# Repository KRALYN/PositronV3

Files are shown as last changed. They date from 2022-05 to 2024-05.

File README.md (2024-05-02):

  

<p align="center">
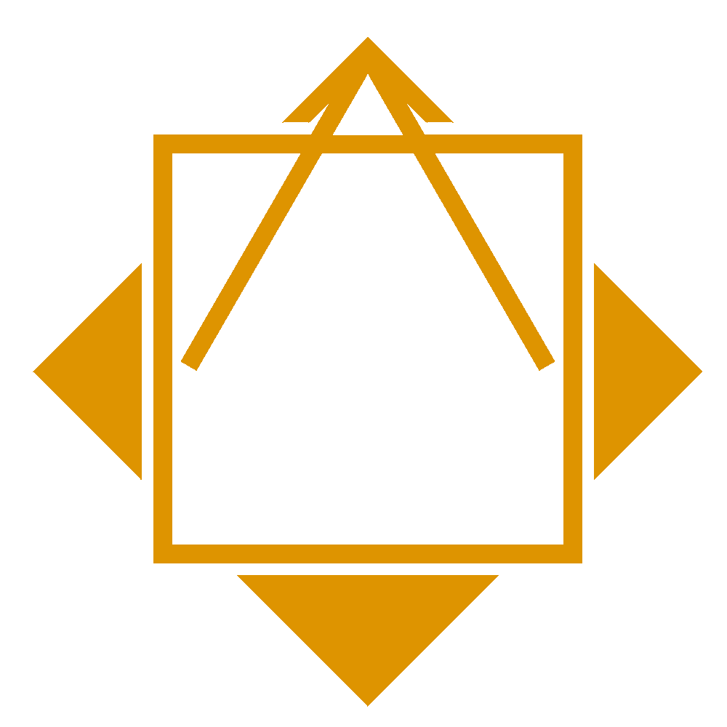
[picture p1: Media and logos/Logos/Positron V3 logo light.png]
   
</p>

---

# This Repo is now set to "LEGACY"
What does this Mean? - The Positron Project has evolved! We now partner with LDO to produce kits for the new and imporved Positron V3.2

This repo will no longer be updated, and will be moved to [the new Github Repo](https://github.com/Positron3D/Positron) once all files are made available from LDO.

Please join the [The Positron Discord](https://discord.gg/5VCruU6EYv) for the most direct updates, and keep an eye on [Our Website](https://positron3d.com).

# PositronV3 LINKS:::

[Positron 3D Website](https://positron3d.com)

[Check out our Youtube to see it in action!](https://www.youtube.com/watch?v=X_QLxTVtyng)

[Source Parts and links from here (BOM)](https://docs.google.com/spreadsheets/d/1M--jvOxUEVNc-NtEsor3uPZQsdXsPD1CKWxmc8fwLWI/edit?usp=sharing) or check out the [Alpha Wiki BOM](https://wiki.positron3d.com/books/general-information-getting-started/page/bill-of-materials-self-sourcing-guide)

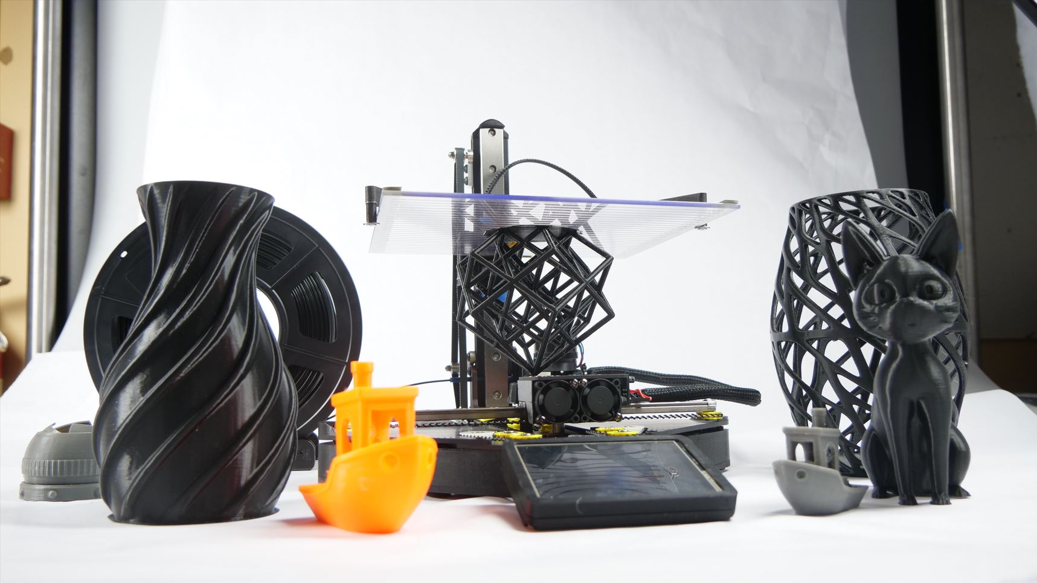
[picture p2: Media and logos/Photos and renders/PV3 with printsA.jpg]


Upside-down, compact, portable, and super fast 3D printer - `Positron V3` has it all. A compact 3D printer that packs into a filament spool box, so you can take it anywhere you want. This design is looking at a 3D printer less like a stationary machine, but more like a powerful tool in a maker/inventor's tool kit. The printer deploys and folds up in less than 90 seconds, fits easily inside a bag, and prints at 200+mm/s.

**Specs**: 
- Max Print Speed: `250mm/s`
- Max Travel Speed: `350mm/s`
- Acceleration: `9800mm/s^2`
- Build Volume: `180x185x180mm`
- Weight: `2700-3100g`
- Hotend max temp: `250C`
- Build Plate Max temp: `90C`
- Power supply: `19-24V; 150-220W`

> Do not treat this design as a finished product. Instead, please see it as a project to be improved upon. When you make this, if you find any improvements, please share it with the community! We could easely have overlooked things; Lets make this printer the best it can be!

>**Disclaimer**: `Positron V3` design is a ***functional*** prototype, not a complete product. **There is absolutely no warranty, and you will make this design at your ***OWN*** risk. We will not be responsible for any damages associated with this design**. 

If you like this design, please consider supporting the Positron 3D team via donations; [Paypal](https://donate.positron3d.com)

# Licenses



**License usage**: `CC-BY`

If you are manufacturing this 3D printer or a close derivative, please put `Positron Logo` visibily on your product and designate `Positron3D` as the inventor of this product. You can find the file inside the logos folder.

On any online postings for any Parts or Kits, please be sure to link back to this github page, as well as to Positron 3D's website.
`https://github.com/KRALYN/PositronV3`
`https://positron3d.com/`

If you made a profit from this design, please consider donating a portion to `Positron3D`. We will be exceedingly grateful.

***All hardware materials and designs provided here are licensed under the [CC-BY-SA-4.0](https://creativecommons.org/licenses/by-sa/4.0/) hardware license.
All documentation, including the Wiki, is under the Creative Commons [CC-BY-SA-4.0](https://creativecommons.org/licenses/by-sa/4.0/) license***.

<div align="center">
Open Licenses
</div>

[Top](#positronv3)

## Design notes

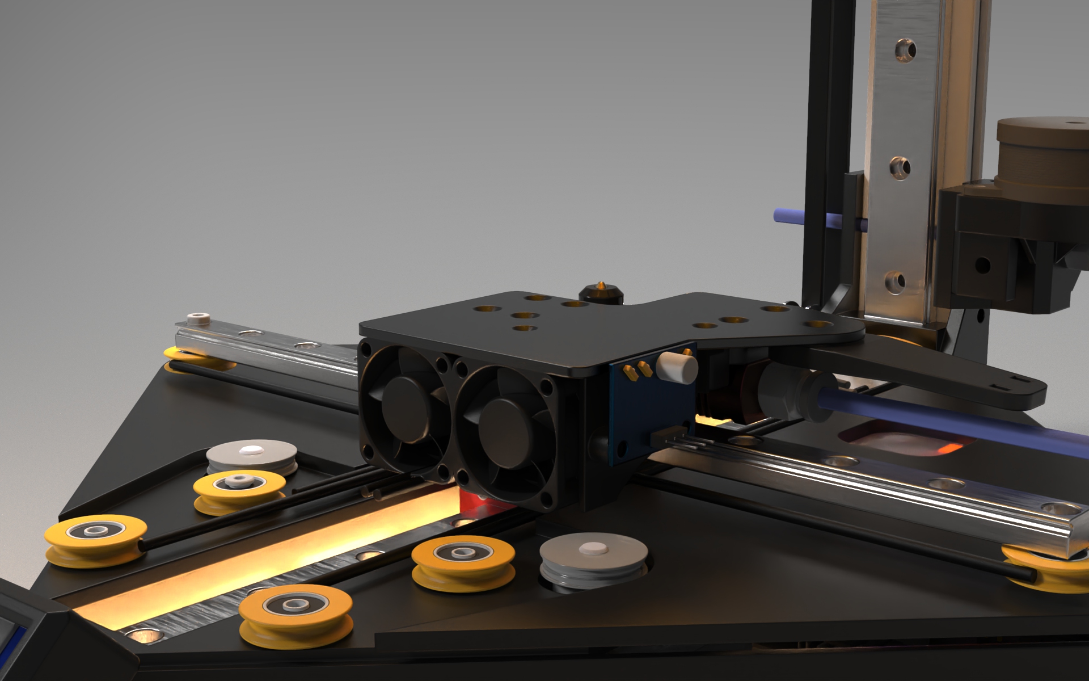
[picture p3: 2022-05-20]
Media and logos/Photos and renders/Postron V3 Render Rev B.656.jpg

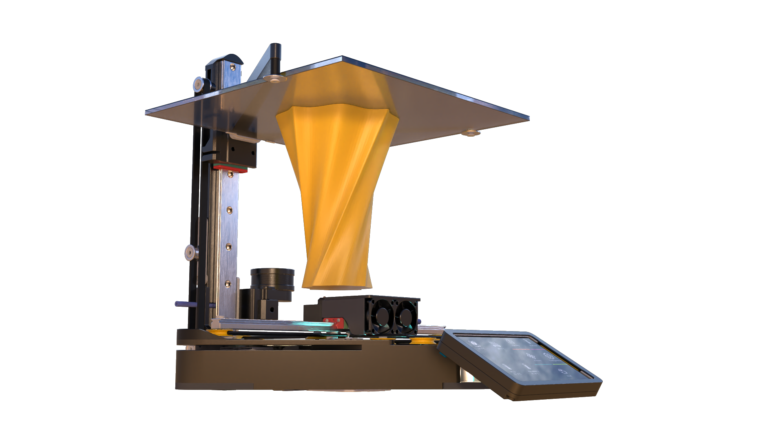
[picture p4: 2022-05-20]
Media and logos/Photos and renders/POSTRON V3 .662.png

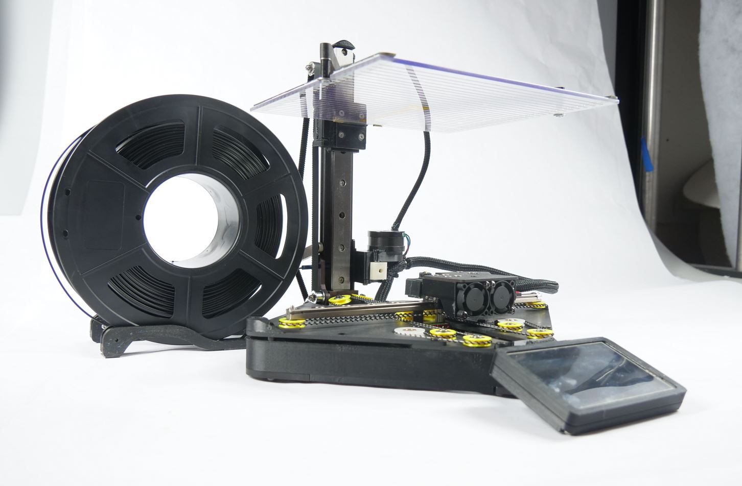
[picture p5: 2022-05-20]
Media and logos/Photos and renders/PV3 Bed High.jpg

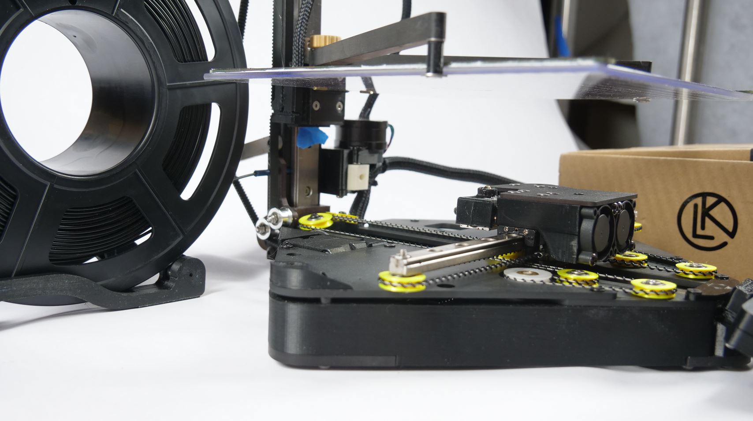
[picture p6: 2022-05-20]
Media and logos/Photos and renders/PV3 Close.jpg

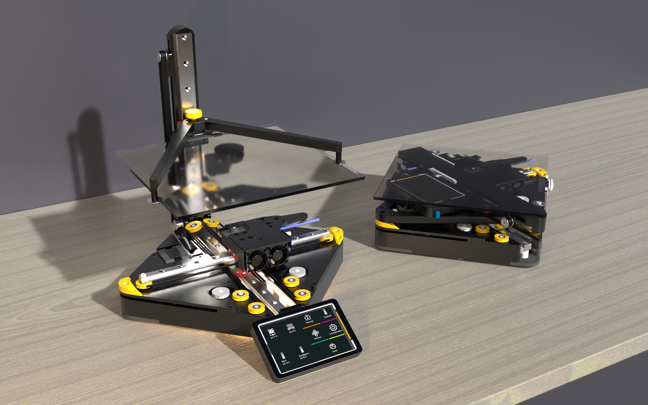
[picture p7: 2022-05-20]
Media and logos/Photos and renders/POSTRON V3 .658.jpg

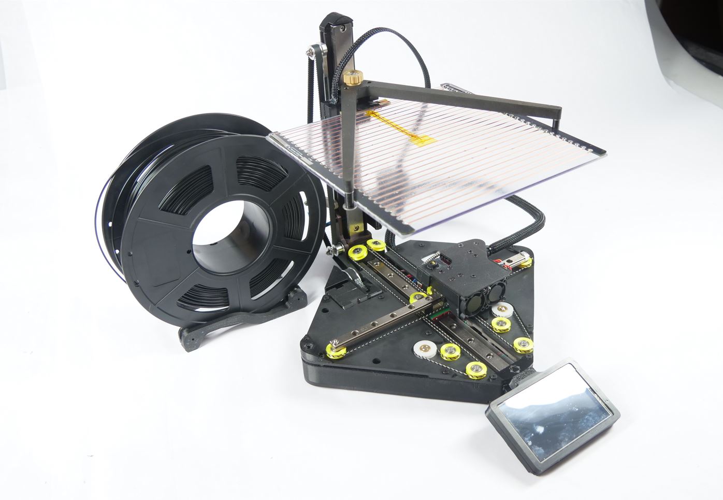
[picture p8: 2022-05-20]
Media and logos/Photos and renders/PV3 ISO.jpg

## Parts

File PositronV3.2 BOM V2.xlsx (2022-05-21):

PositronV3.2 BOM
License: CC BY |  |  | Positron V3 intro video: https://www.youtube.com/watch?v=X_QLxTVtyng
If there is any error, missing parts, or recommendations, please email kralyn3d@gmail.com |  |  |  | Prices may flucuate and not be accurate
All amazon links are affiliates,
Electronics
Number | Name | Purpose/descripton | pcs needed | Link Primary | Cost (Primary Links) | Link Alt (Cheap but slow) | Cost(Cheap but slow) | Total Cost: (Cheaper Link) | Notes:
 | SKR PICO | Control board | 1 | https://amzn.to/3Nm50Lj | 40.99 | https://www.biqu.equipment/products/btt-skr-pico-v1-0 | 28.98 (Sale) | 28.98
 | RPI/Orange Pi | Raspberry pi zero 2W | Pick one | https://www.amazon.com/Raspberry-Zero-Bluetooth-RPi-2W/dp/B09LH5SBPS | TOO EXPENSIVE Right now | https://www.adafruit.com/product/5291 | 15? |  | PLEASE FIND CHEAP SOURCE! Buy at MSRP
 |  | Raspberry pi 4 | Pick One | https://amzn.to/3lxtN37 | TOO EXPENSIVE Right now | https://www.adafruit.com/product/4295 | 30? | 15 | PLEASE FIND CHEAP SOURCE! Buy at MSRP
 |  | Raspberry pi 3 | Pick One | https://www.amazon.com/Raspberry-Pi-3-Model-B/dp/B082QN6L1N | TOO EXPENSIVE Right now | https://www.adafruit.com/product/3055 | 35? |  | PLEASE FIND CHEAP SOURCE! Buy at MSRP
 | Nema 17 20mm | X/Y motor | 2 | https://amzn.to/3G3fPQb | 29.99 | https://www.aliexpress.com/item/1005001303445983.html?ad_pvid=202205191323183466211090998200001325140_1&s=p | 10.71 | 10.71 | 16Ncm
 | Nema 14 28mm | Z Motor | 1 | https://amzn.to/3Nngkab | 21.65 | https://www.aliexpress.com/item/1005002724822207.html | 6.36 | 6.36 | 11Ncm
 | Nema 14 Round | Extruder Motor | 1 | https://amzn.to/3NmFV35 | 20.99 | https://www.aliexpress.com/item/1005002509418988.html | 16.89 | 16.89 | FYSETC 3D Printer Parts 36mm Motor Extruder Stepper Motor 1.8 Angle 0.5A
 | 3.5in TFT GPIO | Touch Screen | 1 | https://amzn.to/3wDS78P | 22.79 | https://www.aliexpress.com/item/4000213494900.html | 2.99 | 2.99
 | IDC 10 pin socket 2.54 | Touch screen connect | 1 | https://amzn.to/3G5ufPU | 5.99 | https://www.aliexpress.com/item/1005001400147026.html | 0.61 | 0.61
 | IDC 10 pin Cable 2.54 | Touch screen power transport | 1 | https://amzn.to/3LwD2LN | 7.99 | https://www.aliexpress.com/item/3256801318866388.html?s=p | 0.41 | 0.41
 | 50W heater cartridge | Heater cartige | 1 | https://amzn.to/3Lw8UjJ | 9.99 | https://www.aliexpress.com/item/2251832656974771.html?pdp_ext_f=%7B%22sku_id%22%3A%2265107791932%22%7D | 1.1 | 1.1
 | NTC 3950K | Temp sensor | 1 | https://amzn.to/3LyQ5w2 | 11.28 | https://www.aliexpress.com/item/3256804109721213.html | 2.39 | 2.39
 | IR bed Probe | IR Probe Differential IR Height Sensor | 1 | https://amzn.to/39ZIREf | 18.99 | https://www.aliexpress.com/item/2251832808870223.html?pdp_ext_f=%7B%22sku_id%22%3A%2266922445346%22%7D | 9.99 | 9.99
 | magnetic connector 6pin | Bed mounting | 1 | https://www.aliexpress.com/item/1005002669709542.html?spm=a2g0o.order_list.0.0.42ea1802lsiPKI | 3.23 |  |  | 3.23 | 90 degree type!!
 | 2510mm Fan 24V | Cooling | 3 | https://amzn.to/3Lp8Lyk | 17.99 | https://www.aliexpress.com/item/32807610078.html | 4.7 | 4.7
 | 5.5x2.1 DC Jack 8A | Power input | 1 | https://amzn.to/3Mv42MX | 7.99 | https://www.aliexpress.com/item/1005003515013042.html?s=p | 0.13 | 0.13 | Use 5.5x2.5 if your power supply is such
 | 24V 8 or 10A power supply | Power supply | 1 | https://amzn.to/3NnZmZ7 | 31.5 | https://www.aliexpress.com/item/1005001946903779.html | 38.2 | 31.5
 | Rocker Switch 10A | Power switch | 1 | https://amzn.to/3LJ4XIB | 6.99 | https://www.aliexpress.com/item/3256802987532702.html?ad_pvid=20220519143050667954035316040001501905_4&s=p | 0.22 | 0.22
 | 24V 3010 Fan Blower | Print Cooling |  | https://amzn.to/3lwK3RW | 9.99 | https://www.aliexpress.com/item/2255800894119261.html?ad_pvid=202205191435593637780472359080001143420_1&s=p | 2.85 | 2.85
 | Kapton Film Heater 200mm 100W | Bed heating Choose one | Pick One | https://www.robotdigg.com/product/877/200mm,-210mm-or-250mm-kapton-film-flexible-heater | 12 |  |  | 12
 | Copper heater strips | Frost Fighter | Pick One | https://frostfighter.com/clear-view-order-guide.htm?add-to-cart=1366&v=402f03a963ba | TOO EXPENSIVE Right now (89 dolars?) |  |  |  | Or find other strips that are 0.02Ω/in
Motion
 | MGN 9C 250mm | X axis rail | 1 | https://amzn.to/3wuJOxm | 20.99 | https://www.aliexpress.com/item/4000264234020.html | 14.72 | 14.72 | 227mm actual, low preload
 | MGN 12C 250mm | Y axis Rail | 1 | https://amzn.to/3G2VnPd | 23.99 | https://www.aliexpress.com/item/4000264234020.html | 14.72 | 14.72 | 235mm actual, low preload
 | MGW 9C 300mm | Z axis rail | 1 | https://www.robotdigg.com/product/955/MGW9-Linear-Rail-and-Carriage | 29 |  |  | 29 | 247mm actual, Medium to high preload
 | GT2 Idler 16T Smooth | Z axis | 4 | https://amzn.to/3wDXZ1R | 11.99 | https://www.aliexpress.com/item/32822906447.html?pdp_ext_f=%7B%22sku_id%22%3A%2264964440436%22%7D | 2.5 | 2.5 | 3mm bore
 | GT2 Low profile Pulley 20T | Z axis | 1 | https://www.aliexpress.com/item/32913757229.html?spm=a2g0o.order_list.0.0.2a3f1802Zv2sCI | 0.72 |  |  | 0.72
 | 48T GT2 Pulley 5mm Bore | Z axis drive train | 1 | https://amzn.to/3Nr7xEg | 12.99 | https://www.aliexpress.com/item/2251832595367020.html?pdp_ext_f=%7B%22sku_id%22%3A%2266985020229%22%7D | 0.53 | 0.53
 | 16T GT2 Pulley 5mm Bore | Z axis drive train | 1 | https://amzn.to/3Nr7xEg | 12.99 | https://www.aliexpress.com/item/2251832595367020.html?pdp_ext_f=%7B%22sku_id%22%3A%2266985020229%22%7D | 0.53 | 0.53
 | GT2 6mm Belt 750mm | Z axis drive train | 1 | https://amzn.to/39zgaOm | 9.99 | https://www.aliexpress.com/item/2251832732634187.html (https://www.aliexpress.com/item/32803353643.html?pdp_ext_f=%7B%22sku_id%22%3A%2267288271232%22%7D) | 2.99 | 2.99
 | GT2 6mm belt loop 130mm | Z axis drive train | 1 | https://amzn.to/3LvUcsL | 11.88 | https://www.aliexpress.com/item/3256803233969258.html (https://www.aliexpress.com/item/2251832785035303.html) | 0.93 | 0.93
 | 5mm Shaft L37mm | Z axis drive train | 1 | https://amzn.to/3a5FwDH | 6.49 | https://www.aliexpress.com/item/2251832241547558.html | 1.64 | 1.64
 | MF115ZZ flanged bearing | Z axis drive train | 2 | https://amzn.to/3wHxTex | 7.49 | https://www.aliexpress.com/item/1005003424591537.html | 7.95 | 7.95
 | BMG drive gear kit | 50T gear with dual gear filament drive | 1 | https://amzn.to/3wFckuN | 21.99 | https://www.aliexpress.com/item/1005001655308475.html | 3.76 | 3.76 | Diy extrder kit
 | 623ZZ Ball Bearing | for Syncromesh Pullies | 12 | https://amzn.to/3yKm5e5 | 13.49 | https://www.aliexpress.com/item/3256803986594273.html?ad_pvid=202205191520509432607776842250001534793_2&s=p | 0.66 | 0.66 | 3x4x10mm
 | Syncromesh Cable 3.81P | SDP/SI name is A 6J 9MAS0805 | 2m | https://shop.sdp-si.com/catalog/product/?id=A_6J_9MAS0805 | 6.61 |  |  | 6.61 | Offical Quote for 1000m is $3.4/m I asked
 | Syncromesh Pulley 3.81P 15T | SDP/SI name A 6P 9M0801505 | 2 | https://shop.sdp-si.com/catalog/product/?id=A_6P_9M0801505 | 22.3 |  |  | 22.3 | Offical Quote for 1000 pcs is $4.79/pcs I asked
Other Mechanical
 | Mk8 heatsink | typically on ender 3 extruder | 1 | https://spool3d.ca/creality-cr-10-heatsink/ | 9
 | Ender 3 heatbreak |  | 1 | https://amzn.to/3PvqYNW | 9.99 | https://www.aliexpress.com/item/3256803118054066.html?ad_pvid=202205191523067573433897611140001583415_1&s=p | 3.28? | 3.28?
 | E3D V6 0.4 nozzle |  | 1 | https://amzn.to/3LJjwMh | 6.59 | https://www.aliexpress.com/item/32827246895.html?pdp_ext_f=%7B%22sku_id%22%3A%2264999741077%22%7D | 0.28 | 0.28
 | capricorn bowden tubing | PTFE tube | 1 | https://amzn.to/3NoMAtp | 9.79 | https://www.aliexpress.com/item/1005001833973163.html | 3.28 | 3.28
 | PC4-M10 PTFT push connector |  | 2 | https://amzn.to/3LAA6xr | 7.99 | https://www.aliexpress.com/item/32895495458.html?pdp_ext_f=%7B%22sku_id%22%3A%2265749709218%22%7D | 0.48 | 04.48?
 | m3x10mm Spacrer Aluminum | Outer dia is 8mm | 8 | https://amzn.to/3MvXLk0 | 11.99 |  |  | 11.99 | Machine down the tube
 | Rubber feet 4mm thick | Bottom feet | 5 | https://amzn.to/3yQ7XzU | 4.98 | https://www.aliexpress.com/item/1005001688504734.html | 3.2 | 3.2
 | 200x200x3mm Borosilicate glass | headed bed body | 1 | https://amzn.to/3MzabaO | 13.99 | https://www.aliexpress.com/item/33045470605.html?pdp_ext_f=%7B%22sku_id%22%3A%2267375853971%22%7D | 14.99 | 13.99
 | 0.25in cable sleeve | need at least 1m | 1 | https://amzn.to/3yKN49n | 8 | https://www.aliexpress.com/item/2255801147284533.html?ad_pvid=202205192036512802097721304800001661795_5&s=p | 0.45 | 0.45
 | M4 ring terminal 22-16 AWG | Crimping syncromesh cable | 2 | https://amzn.to/3luzFKO | 7.99 | https://www.aliexpress.com/item/2251832619804942.html?pdp_ext_f=%7B%22sku_id%22%3A%2264378436063%22%7D | 1.99 | 1.99
 | M4x12 Dowel pin | Bed location 10-15mm acceptable | 2 | https://amzn.to/3NrBJz6 | 6.99 | https://www.aliexpress.com/item/1005003326358562.html?ad_pvid=202205192047085008116476482240002235729_2&s=p | 0.02 | 0.02
 | M3 nylon spacer assortment |  | x | https://amzn.to/3wDTWCP | 12.99 | https://www.aliexpress.com/item/1005003203012157.html?ad_pvid=202205192059301936392797174340002019319_2&s=p | 10.24 | 10.24
 | Zip ties 4in/100mm | Cable management | 2022-10-20 | https://amzn.to/3LxeJgP | 5.5 | https://www.aliexpress.com/item/2251832692914034.html?pdp_ext_f=%7B%22sku_id%22%3A%2265990744133%22%7D | 1.96 | 1.96
 | M3x15 Aluminum Spacer | Motor Mounting | 4 | Same as m3x10mm Spacrer Aluminum |  |  |  |  | Machine down the tube
Fasteners
 | M6x14 thumbscrew 19mm head dia | For Z axis bed arm mounting | 1 | https://www.amazon.com/dp/B07KPDP1HD?s=hi | 13.99 | https://www.aliexpress.com/item/32995228198.html (https://www.aliexpress.com/item/3256801661342209.html) | 2.42 | 2.42 | if you get m6x15 please shave of a mm
 | M5 washer | Z axis holder | 2 | https://amzn.to/38F9luy | 6.99 | https://www.aliexpress.com/item/3256804067235132.html?ad_pvid=20220519211700958809818633940002036878_4&s=p | 0.1 | 0.1
 | M6 nut | Thumbscrew stabilze | 2 | https://amzn.to/3wuwBnY | 3.72 | https://www.aliexpress.com/item/2251832790859685.html?ad_pvid=20220519212820351383008677750001716113_2&s=p | 0.63 | 0.63
 | M4 nut | Z axis mounts | 8 | https://amzn.to/39IXgEY | 6.49 | https://www.aliexpress.com/item/1005001966426139.html | 1.05 | 1.05
 | M4x10 Buttonhead |  | 12 | https://amzn.to/3wBeZG8 | 9.5 | https://www.aliexpress.com/item/32918136753.html?pdp_ext_f=%7B%22sku_id%22%3A%2265960267709%22%7D | 1.39 | 1.39
 | M4x8 buttonhead |  | 2 | https://amzn.to/3LDHVCU | 6.99 | https://www.aliexpress.com/item/10000148429238.html | 1.06 | 1.06
 | M3x6 buttonhead | Find a M3 buttonhead kit | 11
 | M3x20 Buttonhead | Find a M3 buttonhead kit | 2
 | M3x14 Buttonhead | Find a M3 buttonhead kit | 2 | https://amzn.to/3Lq0Fpe | 16 | https://www.aliexpress.com/item/32967225441.html | 2022-02-10 | 7
 | M3x10 Buttonhead | Find a M3 buttonhead kit | 15
 | M3x8 Buttonhead | Find a M3 buttonhead kit | 12
 | M3x25 buttonhead | Find a M3 buttonhead kit | 4
 | M3x12 Buttonhead | Find a M3 buttonhead kit | 5
 | M3 nut 2.4mm | Find a M3 buttonhead kit | 35
 | M3 Washer | Find a M3 buttonhead kit | 12
 | M3x14 Waferhead | Low Wafer Head Machine Screws Flat Head Screw | 17 | https://www.ebay.com/itm/154373020371?chn=ps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 | 2 |  |  | 2
 | M3x12 Waferhead | Low Wafer Head Machine Screws Flat Head Screw | 2 | https://www.ebay.com/itm/154373020371?chn=ps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 | 2 |  |  | 2
 | M3x12 Flathead | Find a M3 Flathead kit | 8
 | M3x18 flathead | Find a M3 Flathead kit | 8
 | M3x10 Flathead | Find a M3 Flathead kit | 1 | https://amzn.to/3wxvXXa | 12.79 | https://www.aliexpress.com/item/32968616563.html | 2022-01-05 | 5
 | M3x6 Flathead | Find a M3 Flathead kit | 2
 | M3x23 Flathead | Can be cut down from M3x25 | 2
 | M3 Nylock Nut | Optional? with thread locker | 2 | https://amzn.to/3wvFwWv | 6.99 | https://www.aliexpress.com/item/2251832799467001.html?ad_pvid=202205192226593765816299021670002129150_1&s=p | 2.07 | 2.07
 | M2.5x8 Flat head |  | 2 | https://amzn.to/3LvfarR | 8.67 | https://www.aliexpress.com/item/3256803068882172.html?ad_pvid=202205192233051883260506929100002345825_4&s=p (https://www.aliexpress.com/item/32900755820.html?ad_pvid=202205192233051883260506929100002345825_3&s=p) | 2.39 | 2.39
 | M2x10 Buttonhead | For Screen | 4 | https://amzn.to/3MzglHU | 6.99 | https://www.aliexpress.com/item/3256803068882172.html?ad_pvid=202205192233051883260506929100002345825_4&s=p | 1.99 | 1.99
 | M3x8 Sockethed | Find a M3 Sockethead kit | 5
 | M3x30 Sockethead | Find a M3 Sockethead kit | 2 | https://amzn.to/3G404bR | 22 | https://www.aliexpress.com/item/2255799876641488.html | 5.72 | 5.72
 | M3x20 Sockethead | Find a M3 Sockethead kit | 7
 | M3x6 threaded insert | Heat press plastic insert | 5 | https://amzn.to/3LxL4UH | 14.99 | https://www.aliexpress.com/item/3256802429609058.html?ad_pvid=202205192244399748035622216640002420224_4&s=p | 2.62 | 2.62
Raw materials/Stock
 | 200x200x4mm AL plate | 6061, 8x8in also works, thickness can be 0.16in | 1 | https://amzn.to/3yTJUAh | 22.99 | https://www.aliexpress.com/item/3256801094393303.html?ad_pvid=202205192158586959024232090060002022455_1&s=p | 16.74 | 16.74 | For base plate and z axis brackets
 | 100x100x2mm AL plate | 6061 T6 | 1 | https://amzn.to/3a1jDFy | 17.99 | https://www.aliexpress.com/item/1005004280302089.html?ad_pvid=202205192158586959024232090060002022455_3&s=p | 4.51 | 4.51 | For Hotend cover and extruder mounting
 | 120x180x3mm AL Plate | 6061 T6 | 1 | https://amzn.to/382e4pT | 16.99 |  |  | 16.99 | For Motor Mounts
 | 220x220x10mm AL plate | 3/8in also works | 1 | https://www.amazon.com/ALUMINUM-SOLID-T6511-Stock-Plate/dp/B01F80W35Q | 30.69 |  |  | 30.69 | For bed arm, bed arm is stackable
 | 30x30x5mm AL angle 90 degree | only 32mm needed | 1 | https://us.misumi-ec.com/vona2/detail/110300466930/?Tab=wysiwyg_area_0 | 7.72 |  |  | 7.72
 | 3010 x250mm AL extrusion | Special, only MISUMI has it. Z axis | 1 | https://us.misumi-ec.com/vona2/detail/110302261730/?Tab=wysiwyg_area_0 | 2.91 |  |  | 2.91 | HFSQN4-1030-250
 | 3mm Black acrylic sheet | 200x300 sheet Sand blasted finish | 1 | https://amzn.to/3Mwj6Kk | 16.95 |  |  | 16.95 | 0.125in also works
 | 3mm Clear Acrylic sheet | 200x60mm Sheet. Sand blasted | 1 | https://amzn.to/3lq6gBt | 13.68 |  |  | 13.68 | 0.125in also works
 | Aluinum Block 6061 | MISC macheing 40x40x70 bar | 1 | https://amzn.to/3wI5uVH | 22.99 |  |  | 22.99
3D printed Parts
 | 3D printed toolhead interconnect | ABS. Prefer SLS nylon | 1
 | Belt and Connector Holder | ABS | 1
 | Edge Raised clamp(Mirror) | PLA/ABS/PETG | 1
 | Edge Raised clamp | PLA/ABS/PETG | 1
 | End Holder Block | ABS/PETG | 1
 | EXP Connector Holder | ABS/PETG | 1
 | Extruder Base | ABS | 1
 | Extruder Cap | ABS | 1
 | Extruder Mid body | ABS | 1
 | Extruder Silder Arm | ABS | 1
 | LED Holder Body | PLA/ABS/PETG | 1
 | Light Clamp Holder | PLA/ABS/PETG | 1
 | M4 spacer 4.1mmx6 | PLA/ABS/PETG | 1
 | Pulley Holder Bottom | ABS/PETG | 1
 | Pulley Holder Top | ABS/PETG | 1
 | Screen holder Base | PLA/ABS/PETG | 1
 | Screen Holder Lid | PLA/ABS/PETG | 1
 | Side Panel Left | PLA/ABS/PETG | 1
 | Side Panel Right | PLA/ABS/PETG | 1
 | Thumbscrew body 3D printed | PLA/ABS/PETG | 1
 | Top Panel Spacers | PLA/ABS/PETG | 1
 | Z axis top stopper | PLA/ABS/PETG | 1
 | 15mm pDia Synchromesh | Prefer Lathed out of Delrin | 10
 | 19.5mm pDia Synchromesh | Prefer Lathed out of Delrin | 2
 | Silicone Mold Bottom (1) | PETG, For hotend Silicone Mold | 1
 | Silicone Mold Bottom | PETG, For hotend Silicone Mold | 1
 | Silicone Mold Top | PETG, For hotend Silicone Mold | 1 |  |  |  |  | 20 | Estimated 3D print material cost
 | JLCPCB Customn PCB | From Github | 1 |  |  |  |  | 35 | around 35 dollars plus SMT
 |  |  |  |  |  |  | Total Cost Estimated: | 532.64 | Dollars | Does not take into account shipping, wires, connectors, materials, time etc

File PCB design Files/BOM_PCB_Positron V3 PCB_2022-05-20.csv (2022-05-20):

ID | Name | Designator | Footprint | Quantity | Manufacturer Part | Manufacturer | Supplier | Supplier Part | Price
1 | XH-2AW_C2908611 | CN3 | CONN-TH_XH-2AW_C2908611 | 1 | XH-2AW | HCTL(华灿天禄) | LCSC | C2908611 | 0.006
2 | 610-92-05GB00 | EXP-10P | CONN-TH_610-92-05GB00 | 1 | 610-92-05GB00 | PINREX | LCSC | C390692 | 0.013
3 | XH-4AW_C2908613 | CN4 | CONN-TH_XH-4AW | 1 | XH-4AW | HCTL(华灿天禄) | LCSC | C2908613 | 0.011
4 | 100nF | C1 | C0603 | 1 | CC0603KRX7R9BB104 | YAGEO | LCSC | C14663 | 0.002
5 | WF2541-WS10E01 | CN1 | CONN-TH_WF2541-WS10E01 | 1 | WF2541-WS10E01 | Wcon(维峰电子) | LCSC | C721503
6 | WS2812B-B/W | LED1,LED2,LED3,LED4,LED7 | LED-SMD_4P-L5.0-W5.0-TL_WS2812B-B | 5 | WS2812B-B/W | worldsemi | LCSC | C2761795 | 0.121
7 | 19-213/Y2C-CQ2R2L/3T(CY) | LED6 | LED0603-R-RD | 1 | 19-213/Y2C-CQ2R2L/3T(CY) | EVERLIGHT | LCSC | C72038 | 0.026
8 | InputHeader | P1,P3 | HEADER-PINS_2.54_04PIN_01ROW | 2
9 | OutputHeader | P2 | HEADER-PINS_2.54_04PIN_01ROW | 1
10 | PTH-Circle | PTH1,PTH2,PTH3,PTH4,PTH5,PTH6,PTH7,PTH8,PTH9,PTH10,PTH11,PTH12,PTH13,PTH14,PTH15,PTH16,PTH17,PTH18,PTH19,PTH20,PTH21,PTH22,PTH23,PTH24,PTH25,PTH26,PTH27 | PTH-CIRCLE.PACK | 27 | Breakout-Hole
11 | 330Ω | R1 | R0603 | 1 | 0603WAF3300T5E | UniOhm | LCSC | C23138 | 0.001
12 | PAD | U1,U2,U3,U4,U8,U9,U10,U11,U12,U13 | PADPAD | 10
13 | 1*6 2.2mmP Magnetic Pogo Pin Connector 3A | U7 | 1*6 2.2P MAGNETIC POGO PIN CONNECOTR | 1 |  |  | Aliexpress
14 | 2*15P 2.54mm copy | H1,TFT | DIP-2.54MM-2X15P | 2 | - | Shenzhen Cankemeng | LCSC | C169817 | 0.132

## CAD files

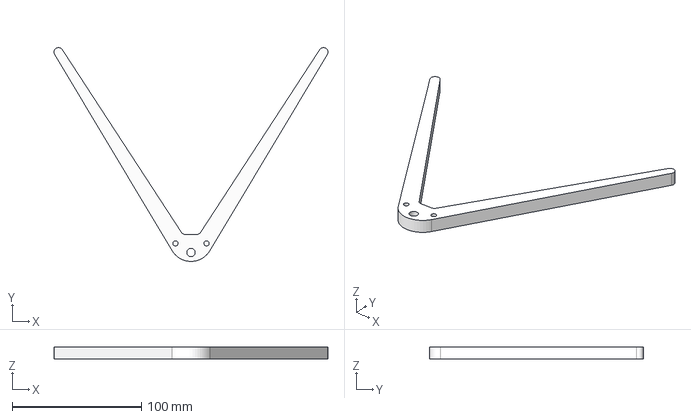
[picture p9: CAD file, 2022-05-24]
CAD files/Custom Metal Parts/Bed Holder Main.step
212.0 x 165.4 x 9.50 mm

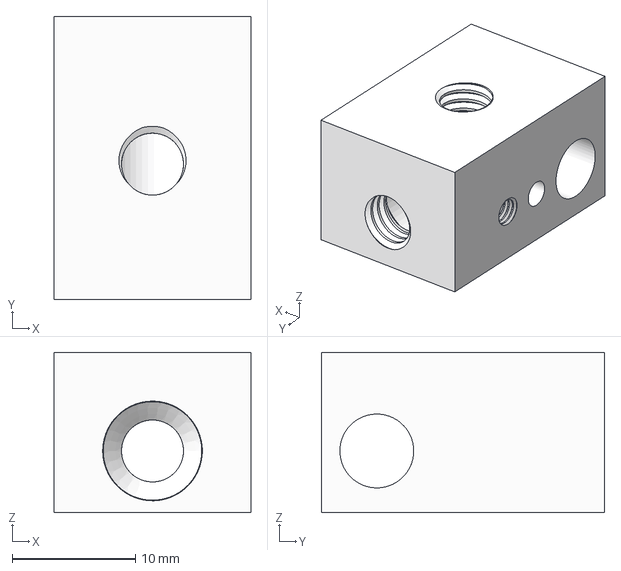
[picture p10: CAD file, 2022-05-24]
CAD files/Acrylic Panel Parts/Hotend block main body.step
16.0 x 23.0 x 13.0 mm

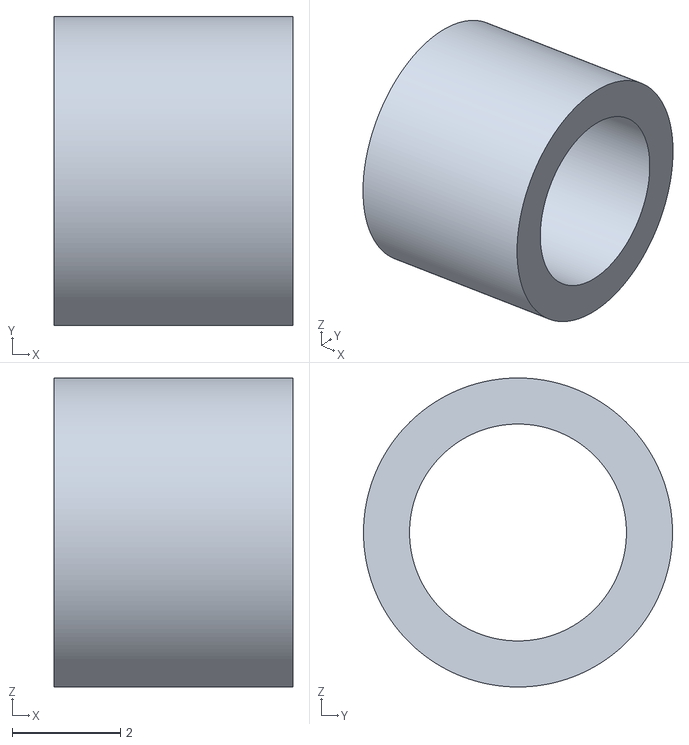
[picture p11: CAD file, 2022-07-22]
CAD files/3D printed Parts/Z axis belt tensioner arm hinge spacer.stl
4.40 x 5.70 x 5.70

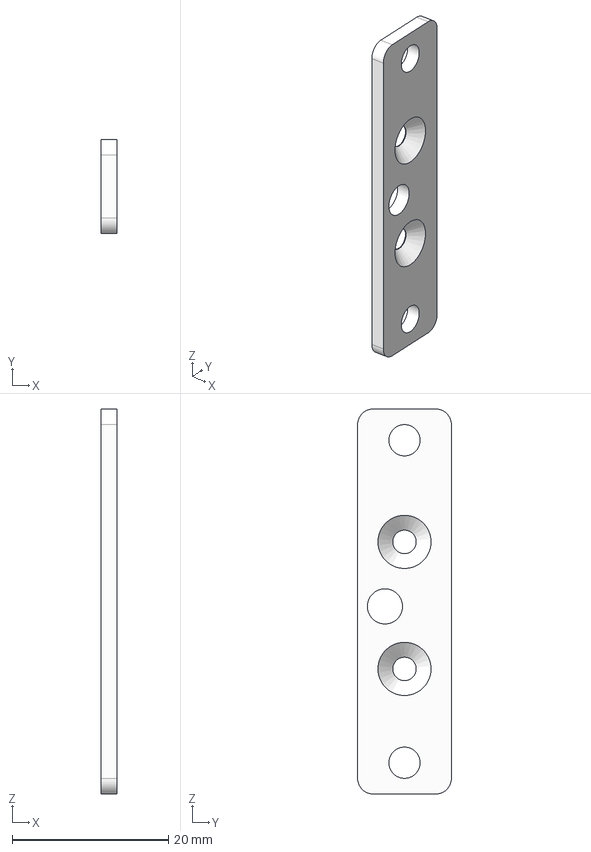
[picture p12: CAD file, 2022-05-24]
CAD files/Acrylic Panel Parts/AL bracket Extruder Mounting.step
2.00 x 12.0 x 49.2 mm

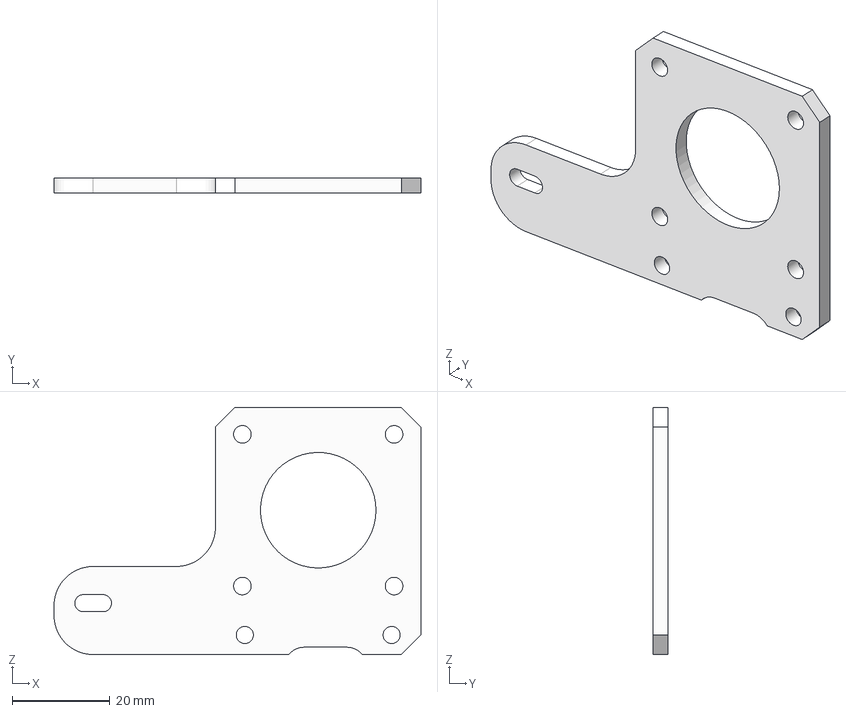
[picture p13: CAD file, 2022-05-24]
CAD files/Custom Metal Parts/Nema 17 holder M3.step
75.0 x 3.00 x 50.5 mm

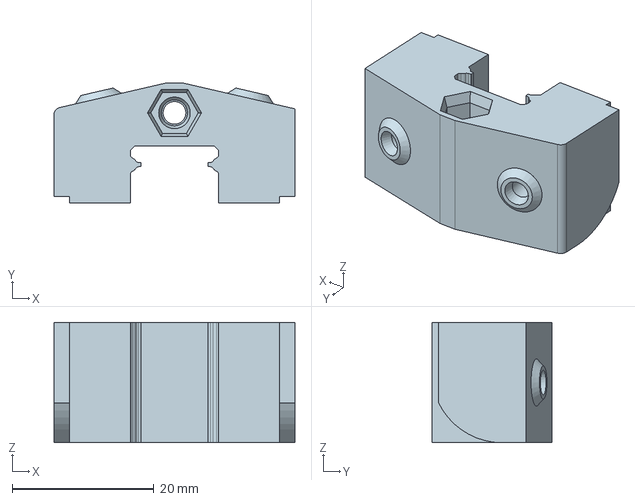
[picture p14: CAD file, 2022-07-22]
CAD files/Z axis tensioner mod/End Holder Block - Tensioning Mod, 1 part, moving ledges.stp
34.0 x 16.9 x 17.0 mm

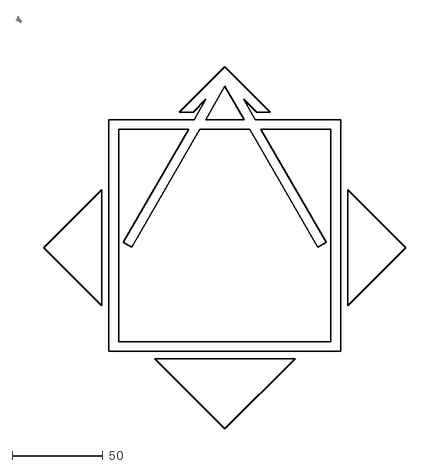
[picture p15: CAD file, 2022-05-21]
Media and logos/Logos/Positron V3 Logo v2.dxf
214.9 x 227.5

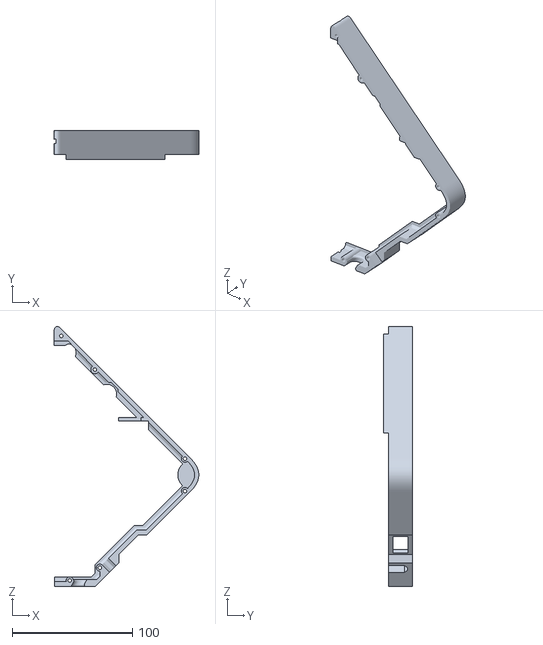
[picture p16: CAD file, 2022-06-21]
CAD files/3D printed Parts/Side Panel Right XT 60.stl
120.6 x 23.8 x 216.6

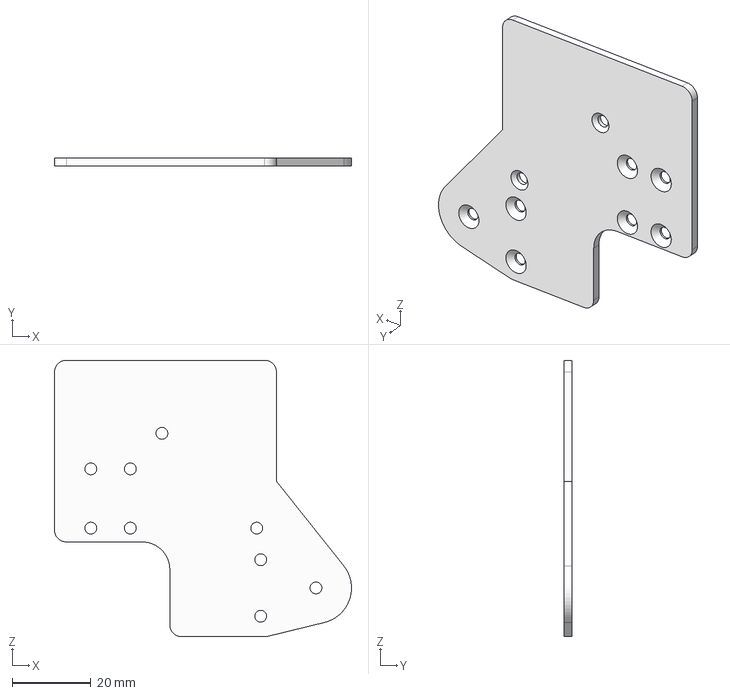
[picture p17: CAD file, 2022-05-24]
CAD files/Acrylic Panel Parts/Toolhead top cover.step
75.2 x 2.00 x 70.0 mm

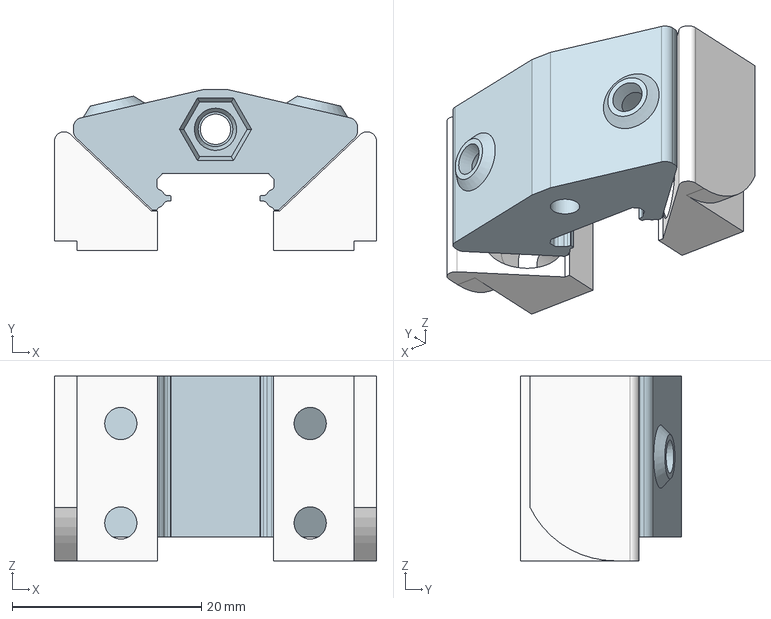
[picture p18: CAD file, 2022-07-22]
CAD files/Z axis tensioner mod/End Holder Block - Tensioning Mod, Fixed Ledges.stp
34.0 x 17.0 x 19.5 mm

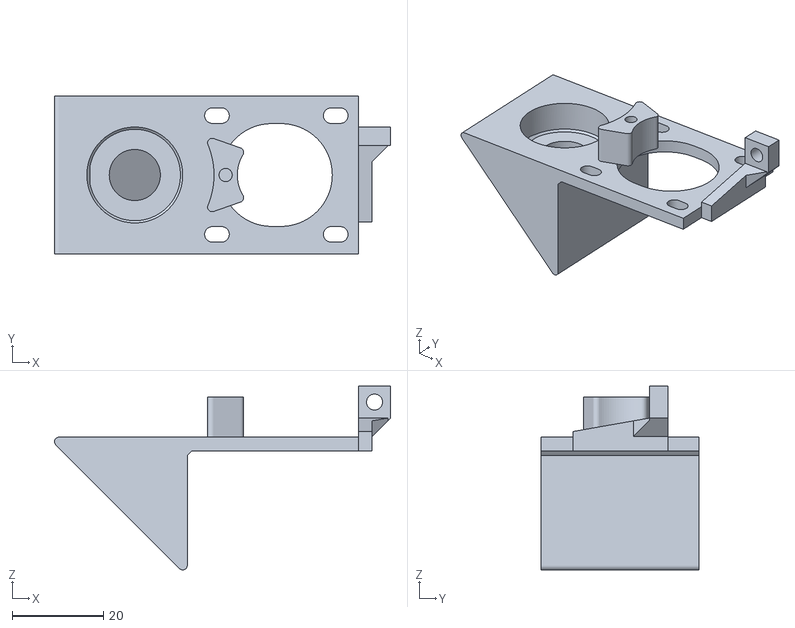
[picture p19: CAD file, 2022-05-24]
CAD files/3D printed Parts/Top Bearing Part.stl
73.6 x 34.5 x 40.3

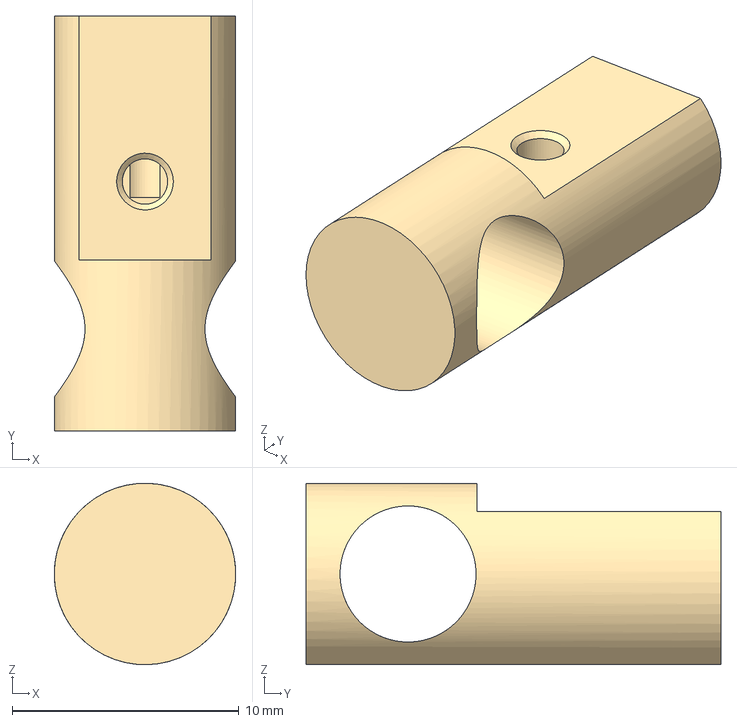
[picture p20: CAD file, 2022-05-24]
CAD files/Acrylic Panel Parts/Hotend Brass Insert.step
8.00 x 18.3 x 8.00 mm

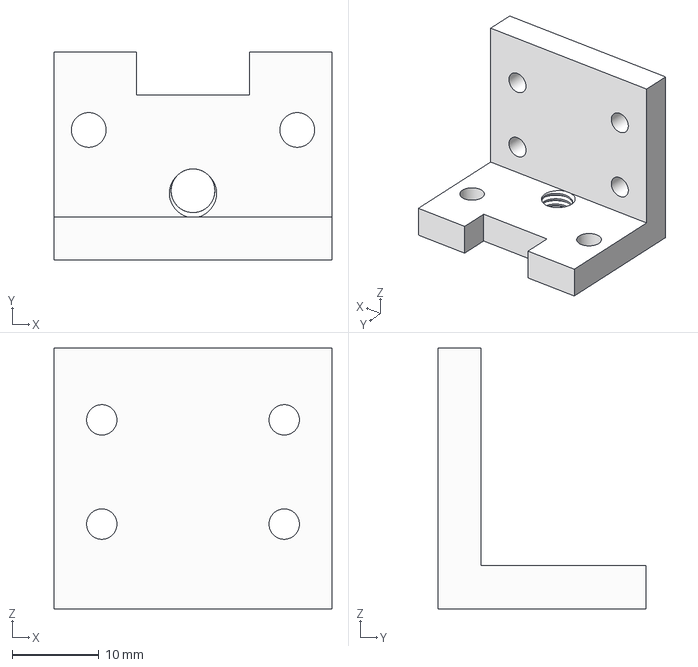
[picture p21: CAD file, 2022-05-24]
CAD files/Custom Metal Parts/90 degree Bed Holder.step
32.0 x 24.0 x 30.0 mm

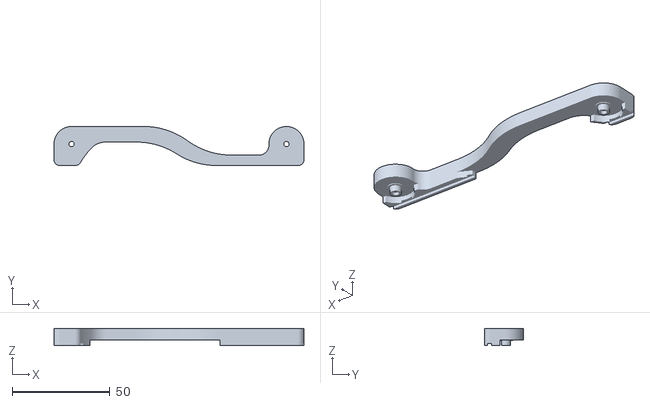
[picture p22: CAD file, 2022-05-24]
CAD files/3D printed Parts/SpoolHolder Part B.stl
128.0 x 20.0 x 8.90

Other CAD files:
CAD files/Custom Metal Parts/Z axis Bottom Holder Left.step
CAD files/3D printed Parts/SpoolHolder Part A.stl
CAD files/Acrylic Panel Parts/Front Y axis Endstop.step
CAD files/Custom Metal Parts/Base Plate.step
CAD files/3D printed Parts/19.5mm pDia Synchromesh.stl
CAD files/3D printed Parts/3D printed toolhead interconnect.stl
CAD files/3D printed Parts/Belt and Connector Holder.stl
CAD files/3D printed Parts/EXP Connector Holder.stl
CAD files/3D printed Parts/Edge Raised clamp(Mirror).stl
CAD files/3D printed Parts/Edge Raised clamp.stl
CAD files/3D printed Parts/End Holder Block.stl
CAD files/3D printed Parts/Extruder Base.stl
CAD files/3D printed Parts/Extruder Cap.stl
CAD files/3D printed Parts/Extruder Mid body.stl
CAD files/3D printed Parts/Extruder Silder Arm.stl
CAD files/3D printed Parts/LED Holder Body.stl
CAD files/3D printed Parts/Light Clamp Holder.stl
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

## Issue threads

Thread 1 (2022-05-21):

Magnetic pogo pins

jmsether, 2022-05-21:
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
I am having a hard time locating the magnetic pogo pins from the BOM I spent about 2 hours searching aliexpress with little to no luck. I am also having a hard time figuring out what the other two parts that are missing are. Are you able to provide any insight into this?

KRALYN, 2022-05-21:
it is the magnetic connector 6pin; I think it is on line 21 in the current
revision. Also, are you sure you are going to order everything before I
upload the build series and instructions?

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

KRALYN, 2022-05-21:
Also, DO NOT SMT Solder the connector! De select them. You are going to
solder wires to the pads.

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

KRALYN, 2022-05-21:
I made BOM more clear in this regard.

jmsether, 2022-05-21:
When you say connector, are you talking about U7? And I was planning on getting the board made and things milled and cut from the file. I can handle some of the milling and all the 3d printing.

Closed 2022-05-21.

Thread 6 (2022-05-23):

Unclear positions in BOM -> 3D printed parts

cyberhuman, 2022-05-23:
Hi. Thank you very much for your project!

I started to source the parts required and noticed a couple of things in the 3D printed parts section:

1. It says "15mm pDia Synchromesh", but I think it's named `Small Synchrmesh Idler.stl` in the repository.
2. There is "M4 spacer 4.1mmx6" x 1. Does "x6" stand for 6 copies of this part?

KRALYN, 2022-05-23:
I see, I’ll fix this soon. Thank you!

On Mon, May 23, 2022 at 10:09 AM Raman Varabets ***@***.***>
wrote:

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

KRALYN, 2022-05-24:
Fixed

Closed 2022-05-24.

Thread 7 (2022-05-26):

BOM list Nema 17 20mm

okaydoke, 2022-05-26:
the cheap link of Nema 17 20mm is pointed to a 40mm motor instead. is that OK to used 40mm?

KRALYN, 2022-05-28:
No, I fixed it. Thank you for finding the error.

Closed 2022-05-28.

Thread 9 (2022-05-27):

Size

antordey51, 2022-05-27:
After uploading 'Z axis belt tensioner arm hinge spacer.stl' for 3d print - I am getting X+Y+Z>30 mm error. I have inputted the measurement (4.4×5.7×5.7) in mm unit- So is there any modification required? Please check images for reference.
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

Also, How do i download the .step files? There's no such option.

KRALYN, 2022-05-27:
Too small, it needs to be bigger. Print a tube then use knife to chop it
down to size

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

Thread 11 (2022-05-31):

ZIP is not ideal in git repositories

ascheucher, 2022-05-31:
Hi KRALYN!

That's an awesome project! I am really tempted to rebuild the printer, but let's see whether I find time for that.

Just something I noticed, during checking your repo: ZIP files are not encouraged in git repositories.
You will lose the possibility to track changes and also AFAIK, git compresses everything anyway on transfer and storage.
It's just only drawbacks checking in zipped files.

Thanks for sharing your project!

ascheucher, 2022-06-01:
Never used git lfs, but this sounds like the proper way to do it.

luminous-flux, 2022-06-02:
It works well for CAD - it just tells git to treat the files as pure binary
blobs so it doesnt try to diff them as text with previous versions.

On Wed, Jun 1, 2022 at 5:32 PM Andreas Scheucher ***@***.***>
wrote:

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

KRALYN, 2022-07-22:
I think this application of Zip is fine since it is an CAD assembly.

Closed 2022-07-22.

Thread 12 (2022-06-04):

Need clarification

antordey51, 2022-06-04:
This is in regards to Raw materials/Stock parts available in github repository.

In the parts sourcing excel sheet - In row 109 :

Aluinum Block 6061 MISC macheing 40x40x70 bar1

https://amzn.to/3wI5uVH

The size mentioned in the sheet is 40×40×70 (I assume in mm) but in the provided Amazon link- the size of the AL bar is 50mm×50mm×150mm.

Well, I need a clarification regarding this size issue. Does or doesn't the size matters? If I order from that Amazon link- the size will be bigger than required according to the sheet. So do I have to cut it later to match the size? Honestly, instead of doing that myself, I will better order a customized one if size really matters.

antordey51, 2022-06-04:
@KRALYN

cyberhuman, 2022-06-05:
I think it just needs to be 40x40x70mm or bigger.

KRALYN, 2022-07-22:
The stock sizes are just recommendations, I'll make this clear in the BOM

Closed 2022-07-24.

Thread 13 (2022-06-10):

Specifications

antordey51, 2022-06-10:
  | BEDHEATERFILM1 | Kapton Film Heater 200mm 100W | Bed heating

For this part- the first link is of robotdigg & there's 6 options to choose from :
PL2020-12V
PL2121-12V
PL2525-12V
PL2020-24V
PL2121-24V
PL2525-24V

Please specify which one should we get. I cross checked with price to find a match but all options cost the same 12 USD & you haven't specified the voltage.

KRALYN, 2022-06-10:
Hello, it is 24V, 100W heater, so it should be PL2020-24V. I’ll add this
spec in.

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

Closed 2022-06-10.

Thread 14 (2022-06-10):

Materials Specifications

antordey51, 2022-06-10:
For printing the Acrylic Panel Parts & as well  Custom metal parts - which technology should be used?
•CNC Machining
•Sheet Metal
Also which material should be used?
•Aluminium 5083/5754/6082
•Steel S235JR/St52/S355
•Stainless Steel V2A/V4A

Or Everything can be printed in industrial/commercial plastics? If it can be done using plastics instead of Aluminium/Steel- that would really be cost saving.

Your input would really be helpful for whoever doing this project without any experience, Thanks.

KRALYN, 2022-07-22:
I designed and simulated everything with their respective materials. For the manufacturing method; I think any method that satisfies the geometry and according to the engineering drawings would be sufficient. I think 6000 series Aluminum should work, the 5000 series Aluminum might be a bit weak. I real testing would needed to be done inorder to ensure the functions of the alternative materials.

Closed 2022-07-24.

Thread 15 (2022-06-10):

Printing Materials

antordey51, 2022-06-10:
For printing the Acrylic Panel Parts & as well  Custom metal parts - which technology should be used?
•CNC Machining
•Sheet Metal
Also which material should be used?
•Aluminium 5083/5754/6082
•Steel S235JR/St52/S355
•Stainless Steel V2A/V4A

Or Everything can be printed in industrial/commercial plastics? If it can be done using plastics instead of Aluminium/Steel- that would really be cost saving.

Your input would really be helpful for whoever doing this project without any experience, Thanks.

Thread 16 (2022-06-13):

Copper heater strips

antordey51, 2022-06-13:
HEATERSTRIP1

Row 28 : Copper heater stripsFrost Fighter | Pick One

TOO EXPENSIVE Right now (89 dolars?)

Well, Whilst making the list- you had possibly found the price is 89 USD. The link(https://frostfighter.com/clear-view-order-guide.htm?add-to-cart=1366&v=402f03a963ba) you've added to the sheet- directly adds the item to cart and it shows $149 as of now.

So, Could you please revisit and confirm if this the same item with increased price or attach the actual product link- otherwise there's a chance others who can afford this may buy the wrong one which might not be useful:(

KRALYN, 2022-07-22:
The idea is that eventually that there would be a film heater that users just stick on and not bother with the strips. The Frostfighter strips are only for prototyping.

Closed 2022-07-24.

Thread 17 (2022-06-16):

Found the 1030 on AliExpress

18Markus1984, 2022-06-16:
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

I found the 1030 extrusion on [AliExpress ](https://de.aliexpress.com/item/1005001957312144.html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) maybe you can add the link to the BOM. The size values are at some points a little different, but shouldn't be bothering the build.
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

KRALYN, 2022-07-22:
Very nice! I think this piece will work as well. I'll add it into the BOM

antordey51, 2022-07-24:
@18Markus1984 isn't the one from misumi cheap around 3 USD? I checked the Aliexpress link and for 250mm- it's around 9 USD:(

18Markus1984, 2022-07-24:
> @18Markus1984 isn't the one from misumi cheap around 3 USD? I checked the Aliexpress link and for 250mm- it's around 9 USD:(

Yes but not shippeable to Europe

Closed 2022-07-22.

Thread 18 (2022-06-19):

Need engineering/technical drawing for the 90 degree Bed Holder

Owen12121212121, 2022-06-19:
The "90 degree Bed Holder.step" in "Custom Metal Parts" is missing an engineering/technical drawing as of 6/18/2022.

Closed 2022-06-28.

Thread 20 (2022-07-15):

Missing "Pulley Holder Bottom" and "M4 spacer 4.1mmx6" stl files.

Owen12121212121, 2022-07-15:

KRALYN, 2022-07-22:
updated BOM name M4 spacer 4.1mmx6 to Z axis belt tensioner arm hinge spacer.
Pulley holder was an assembly and it was removed. Thank you for pointing things out!

Closed 2022-07-22.

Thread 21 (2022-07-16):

What is the Hotend Heater block? Can't find it on BOM.

Owen12121212121, 2022-07-16:

FramingApp, 2022-07-18:
It has to be manufactured yourself or purchased through a supplier once they become available in the future. Watch the video here: [Hotend Segment of PostronV3 video](https://youtu.be/X_QLxTVtyng?t=1329)
If you want to get hold of a manufactured hotend ASAP, get in touch with @slicingblade on discord. He might be able to sort you out as he is manufacturing and selling kits himself.

KRALYN, 2022-07-22:
I created Machined Parts-from Stocks section in BOM and all machined part names are listed within.

Closed 2022-07-22.

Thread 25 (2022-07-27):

Extruder Motor Compatibility for 0.9° Angle

antordey51, 2022-07-27:
In BOM :

MOTOREXTRUDE | Nema 14 Round | Extruder Motor | 1 | https://amzn.to/3NmFV35 | 20.99 | https://www.aliexpress.com/item/1005002509418988.html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 | 16.89 | 16.89 | FYSETC 3D Printer Parts 36mm Motor Extruder Stepper Motor 1.8 Angle 0.5A |  
-- | -- | -- | -- | -- | -- | -- | -- | -- | -- | --

MOTOREXTRUDE
	Nema 14 Round	Extruder Motor	1
Two Marketplace links available.
	Amazon.com costs : 20.99 USD
        Aliexpress.com costs : 16.89 USD
Description : FYSETC 3D Printer Parts 36mm Motor Extruder Stepper Motor 1.8 Angle 0.5A

Well, I have found similar one from stepperonline.com - Round Nema 14 Bipolar 0.9deg 7Ncm (9.91oz.in) 0.5A 8.5V 36x12mm 4 Wires(https://www.omc-stepperonline.com/round-nema-14-bipolar-0-9deg-7ncm-9-91oz-in-0-5a-8-5v-36x12mm-4-wires-14hr05-0504s). However, Clearly this one is 0.9 degree Angle unlike the recommended 1.8° Angle from FYSETC- So, Just wanted to confirm if this 0.9° Angle one from stepperonline will be compatible with the setup with any workaround or the 1.8° Angle one from FYSETC must be used?

CtrlAltNoot, 2022-11-04:
I haven't completed a Positron build yet (as I've been continually pre-occupied with other small projects); however from my experience, as long as the originally specified stepper and the one you're replacing it with share the same form factor, any stepper can be used. You just need to change your Klipper config to reflect that. https://www.klipper3d.org/Rotation_Distance.html

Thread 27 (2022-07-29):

Integrate PR's into main CAD

FramingApp, 2022-07-29:
Unfortunetley my PR's from last week were loose files. I was not able to include them in the main STEP as i do not have f360.
The files are under
CAD/NX
and
CAD/Angled Extruder Mod

It would probably be best if these files were properly integrated into the main CAD files if possible.

Closed 2022-08-14.

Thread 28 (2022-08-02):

Hotend Brass Insert.step and Hotend block main body.step files in wrong location.

Owen12121212121, 2022-08-02:
They are in the The Acrylic Panel Parts file.

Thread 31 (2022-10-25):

Bed Magnetic Connector in Wiring Diagram is flipped

Alix1723, 2022-10-25:
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

The PNG currently in the Electronics folder has the two lowest (square side) pins wired to Bed +/-, but the instruction video and the bed connector PCB have the thermistor pins lowest (square side) and the bed pins highest (round side)

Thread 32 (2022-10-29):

Integrate the Tensioner into the main CAD

FramingApp, 2022-10-29:
Hi KRALYN,

What do you think about integrating the [Tensioning mod part](https://github.com/KRALYN/PositronV3/blob/main/CAD%20%20files/Z%20axis%20tensioner%20mod/End%20Holder%20Block%20-%20Tensioning%20Mod%2C%201%20part%2C%20moving%20ledg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) into the main CAD and engineering drawings (1 csk hole required in the 90 degree z axis mount part)?

Or at the very least, the other two files in the Tensioning mod folder are not required anymore after testing. They and are confusing people and should be removed. (ie, remove [this file](https://github.com/KRALYN/PositronV3/blob/main/CAD%20%20files/Z%20axis%20tensioner%20mod/End%20Holder%20Block%20-%20Tensioning%20Mod%2C%20Fixed%20Ledges.stp) and [this file](https://github.com/KRALYN/PositronV3/blob/main/CAD%20%20files/Z%20axis%20tensioner%20mod/Z%20axis%20Holder%20block.prt))

Regards,
Harry

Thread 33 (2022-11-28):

had trouble opening the assembly STEP, but solved after implementing fix

Sorsly, 2022-11-28:
Using SolidWorks Premium 2021 SP4.1, ran into "Encountered invalid record index” error after unzipping and attempting to import the [full assembly STEP file](https://github.com/KRALYN/PositronV3/blob/main/CAD%20%20files/Positron%20V3.2%20Rev%20B%20SHOW%20ALL%20v57%20STEP.zip).

This [troubleshoot article](https://www.javelin-tech.com/blog/2018/11/encountered-invalid-record-index-solidworks/) helped fix the file and allowed me to import.

In my default configuration, 3D Interconnect was already deactivated. The fix was replacing text.

c/p for convenience:

1. Deactivate “[3D Interconnect](https://www.javelin-tech.com/blog/tag/3d-interconnect/)” in SOLIDWORKS Options > System Options > Import
2. Open the STEP file using text editor such as Notepad. The file will open as text.
3. Use Search/Find, and search for: "PRESENTATION_STYLE_ASSIGNMENT". If this problematic data is found, replace it using the Search/Find & Replace command with: "PRES"
4. Save the file. This parameter will now be skipped during the import’s parsing process, and thus the warning will not display and the STEP should import as expected.
5. Retry the Import into SOLIDWORKS.

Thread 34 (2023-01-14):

Pulley holder bottom is missing from latest, currently only found in revert-3-main

pixelated-being, 2023-01-14:
the file is not found in the latest of all commits.

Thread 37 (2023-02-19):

Why is the hotend limited to 250C? Is it PTFE-lined?

kozross, 2023-02-19:
The title says it all - it seems kind of odd to have a limit like this for any other reason. If the hotend is indeed PTFE-lined, it seems like a very odd choice, since it means you can't print anything other than PLA, really.

metaxis, 2023-02-19:
petg, pctg, asa, abs, tpu, hips, sbs, pva all print well at 250 C and below.  Where did you hear you can only print PLA below 250C?

kozross, 2023-02-19:
@metaxis - ASA needs 260 in practice, and is in fact the recommended temperature by at least one manufacturer. I literally had layer delamination and cracking at 250 with Prusament ASA. PETG can print below that, but you need to go above 250C to get any decent flow - again, speaking from experience. I haven't printed PCTG, ABS, TPU or HIPS, but from a casual glance, many manufacturers of such filaments suggest temps _well_ above 250.

Regardless, my question stands.

nomadsgalaxy, 2025-01-07:
This is super late - hello from 2 years later; Yes, it's because the PTFE tube presses against the heatbreak, and we don't want people to risk getting toxic fumes inhaled. The new 3.2 hotend is easily able to hit 300c, but the PTFE is the dangerous part.

See the latest version of the project here; https://github.com/Positron3D/Positron

Closed 2025-01-07.

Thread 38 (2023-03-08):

Availibility for syncromesh Pulleys is terrible. Is this a viable alternative?

Wdfitzpat007, 2023-03-08:
The syncromesh pulleys have an 8wk lead time and are expensive.

3D printed pulleys have grub screw issues

Why not 3D print a GT2 20tooth pulley to Syncromesh 3.81mm 15tooth adapter?

Sure you will need to face the GT2 Pulley to get it to the same height... but compared to waiting weeks and blowing $20/pulley??? Also if you can print ABS and you get Nano polymer adhesive, you can print them in POM. Sure it smells nasty while its printing, but it gives a good result

Too bad the rods coming out of the NEMA 17 motors are round, would be easy to print friction fit pulleys. Qiditech from china uses friction fit plastic pulleys if I remember correctly, but theirs are injection molded.

Here is what I came up with:

[https://drive.google.com/file/d/1s4UBSseel5fdsOtHoDCnQ9t1MehNmwnG/view?usp=sharing](url)

nomadsgalaxy, 2025-01-07:
This is super late - but we've moved to 3mm belts instead. See the latest version of the project here;  https://github.com/Positron3D/Positron

Closed 2025-01-07.

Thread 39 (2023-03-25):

May I please refer to your design in my project?

ASRT9, 2023-03-25:
May I please refer to your design in my project?

RCPlayland, 2023-03-30:
Yes you may.  Also be sure to include the original designer as well.  His link is in my description
    On Saturday, March 25, 2023 at 09:11:16 AM CDT, ASRT9 ***@***.***> wrote:

May I please refer to your design in my project.

—
Reply to this email directly, view it on GitHub, or unsubscribe.
You are receiving this because you are subscribed to this thread.Message ID: ***@***.***>

RCPlayland, 2023-03-30:
That is if it is a re-design.

I do have a couple originals.

Which design is it that you are referring to?
    On Saturday, March 25, 2023 at 09:11:16 AM CDT, ASRT9 ***@***.***> wrote:

May I please refer to your design in my project.

—
Reply to this email directly, view it on GitHub, or unsubscribe.
You are receiving this because you are subscribed to this thread.Message ID: ***@***.***>

nomadsgalaxy, 2025-01-07:
Hello, I know this is late, but yes - this is open source, so you can always reference this as long as you follow the creative commons licensing.

Please see the latest version of the project here; https://github.com/Positron3D/Positron

Closed 2025-01-07.

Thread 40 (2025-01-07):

CAD Models design files needed for improved printability.

SeverinStahl, 2025-01-07:
Would it be possible to upload the design files for the "3d printabel toolhead interconnect" and "extruder mid body" I noticed that some walls are really thin sub 0.5 mm and would like to increase the wall thickness on these parts especially for nylon printing.

nomadsgalaxy, 2025-01-07:
Hello Severin, this repo is no longer active, please see the latest version of the Positron here; https://github.com/Positron3D/Positron

SeverinStahl, 2025-01-07:
Do I find there as well the "legacy" files?
Since to my knowledge the V3.2 has a completely different extruder assembly compared to V3

nomadsgalaxy, 2025-01-08:
Yes, the 3.2 uses a orbital style Extruder.

However, Kralyn and The Positron team are no longer supporting the V3, as there were many bugs with it that were fixed in the V3.2

SeverinStahl, 2025-01-11:
Sure that's what they write. But isn't the idea behind open source projects that's everyone can contribute and has the availability of the full source in case some changes might be needed?
Sure I can reverse engineer this part amd draw it in CAD myself but this seems counterintuitive when considering that the design files are on some hard drives already 😅

Anyway thanks for the response!

Closed 2025-01-07.

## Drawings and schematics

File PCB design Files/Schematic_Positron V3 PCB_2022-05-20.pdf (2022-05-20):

# Square 2x2 LED array

# Front LED array

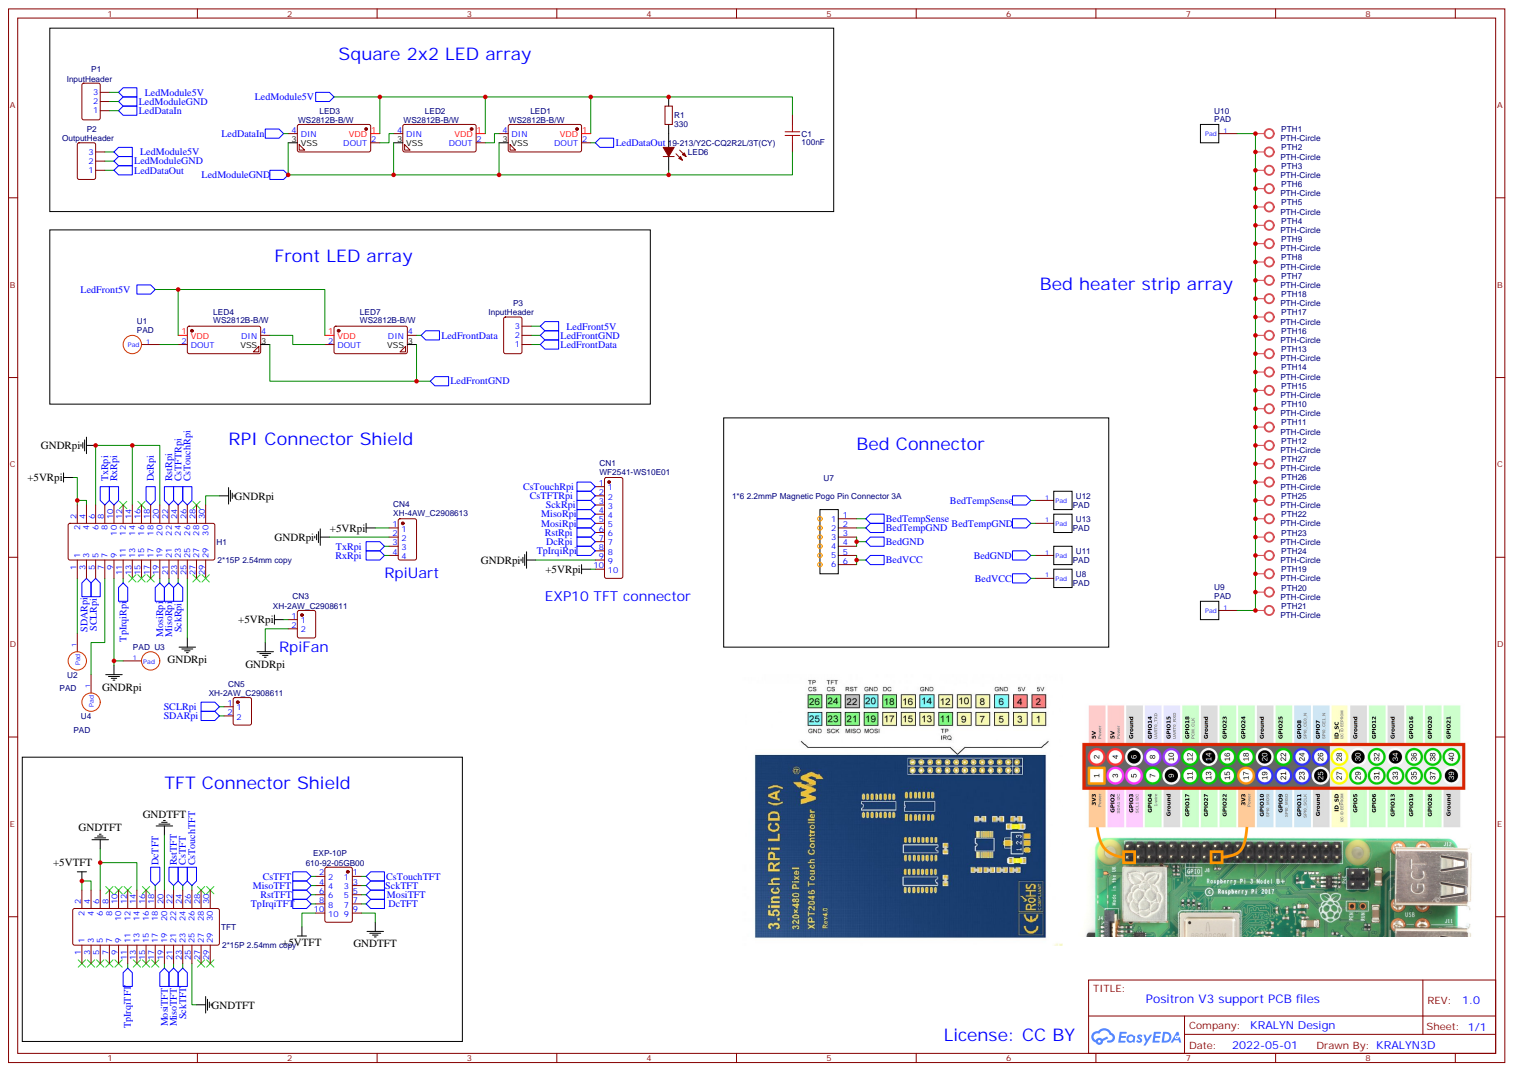
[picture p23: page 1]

Bed heater strip array

1*6 2.2mmP Magnetic Pogo Pin Connector 3A

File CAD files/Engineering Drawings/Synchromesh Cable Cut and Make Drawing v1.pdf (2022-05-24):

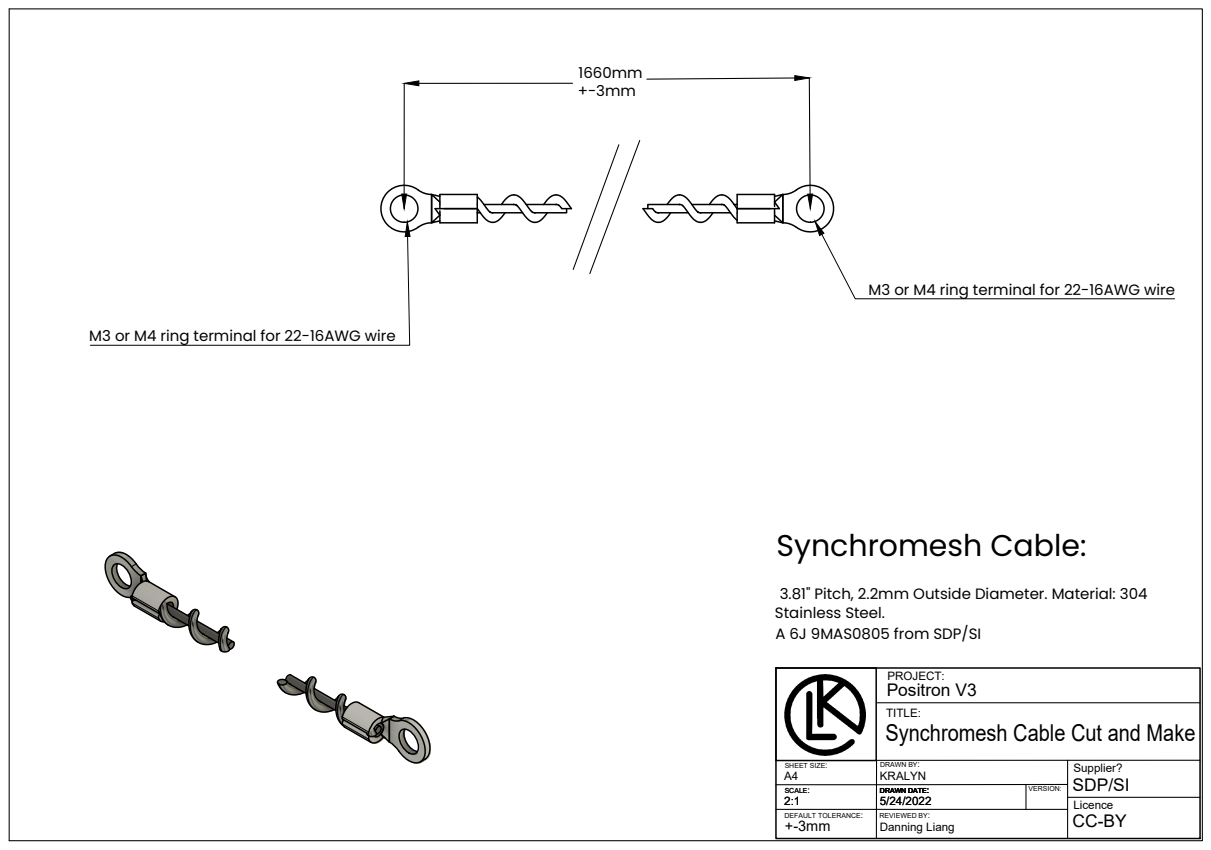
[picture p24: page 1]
DRAWN BY: SCALE:; DRAWN DATE:; VERSION: REVIEWED BY:; Synchromesh Cable:

M3 or M4 ring terminal for 22-16AWG wire

3.81" Pitch, 2.2mm Outside Diameter. Material: 304
Stainless Steel.
A 6J 9MAS0805 from SDP/SI

PROJECT:
Positron V3
Synchromesh Cable Cut and Make

TITLE: SHEET SIZE: SCALE: DEFAULT TOLERANCE:

A4 | KRALYN | Supplier? SDP/SI

2:1 | 5/24/2022
+-3mm | Danning Liang

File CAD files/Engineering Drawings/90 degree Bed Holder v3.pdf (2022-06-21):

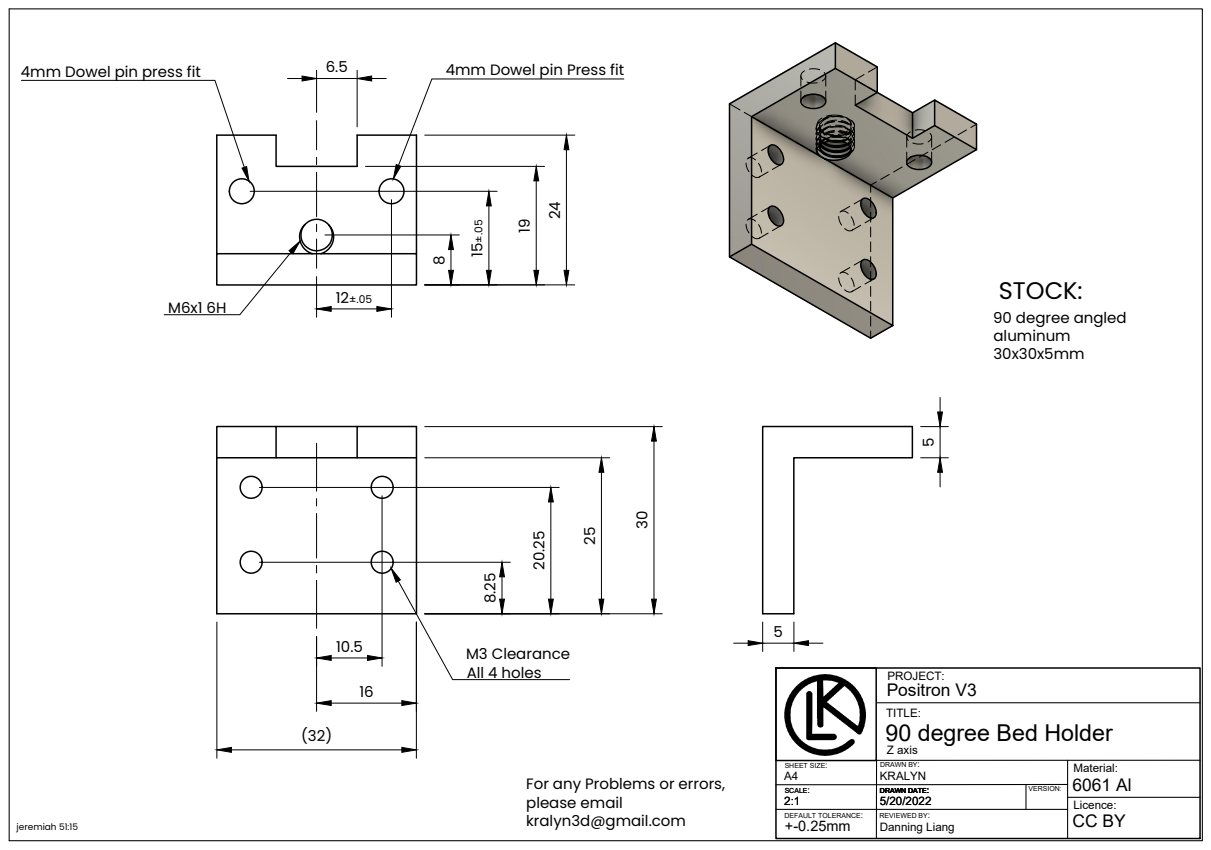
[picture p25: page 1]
DRAWN BY: SCALE:; DRAWN DATE:; VERSION: REVIEWED BY:; Z axis; M3 Clearance All 4 holes; 4mm Dowel pin press fit; 4mm Dowel pin Press fit; jeremiah 51:15; kralyn3d@gmail.com; 90 degree angled

PROJECT:
Positron V3
90 degree Bed Holder

TITLE: SHEET SIZE: SCALE: DEFAULT TOLERANCE:

A4 | KRALYN | Material: 6061 Al

For any Problems or errors,
please email

2:1 | 5/20/2022
+-0.25mm | Danning Liang

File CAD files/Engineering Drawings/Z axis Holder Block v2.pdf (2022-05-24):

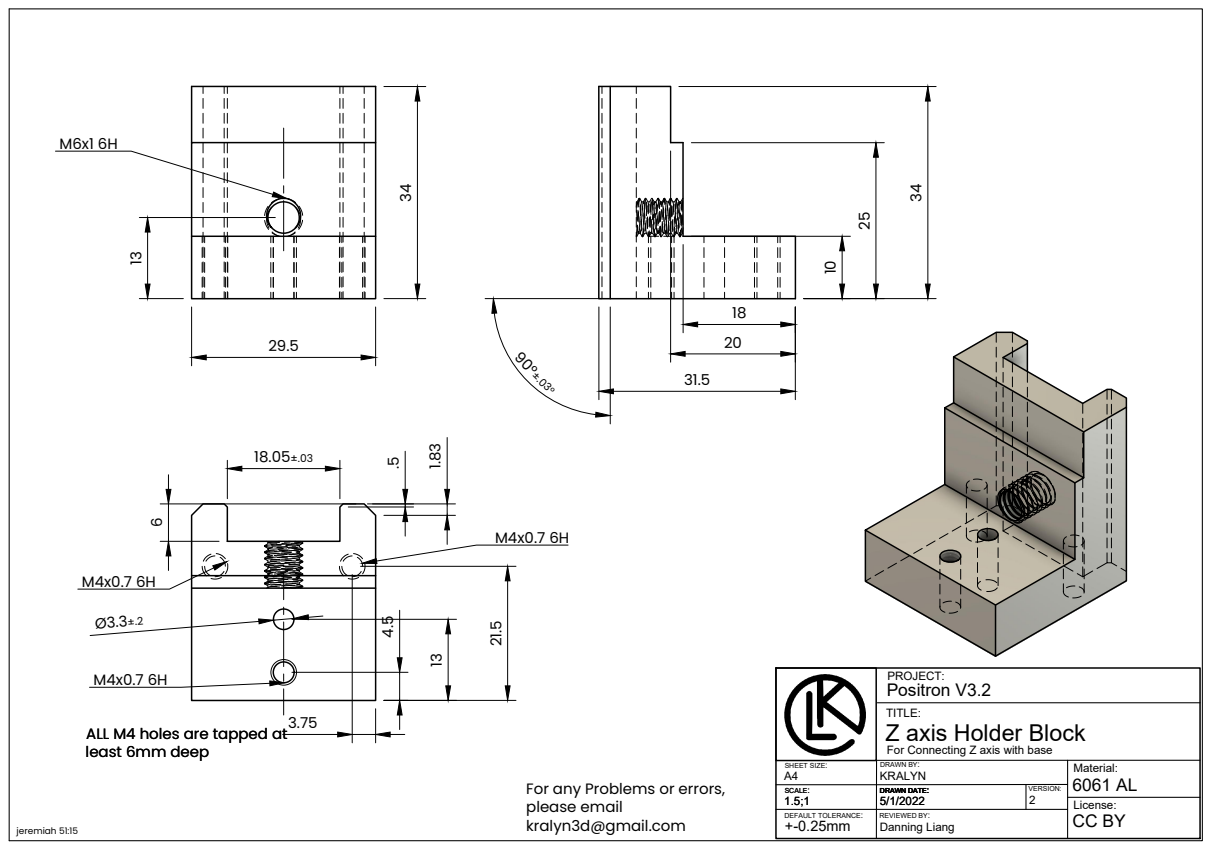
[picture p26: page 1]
DRAWN BY: SCALE:; DRAWN DATE:; VERSION: REVIEWED BY:; jeremiah 51:15; kralyn3d@gmail.com

PROJECT:
Positron V3.2
Z axis Holder Block

TITLE: SHEET SIZE: SCALE: DEFAULT TOLERANCE:

ALL M4 holes are tapped at
least 6mm deep

For Connecting Z axis with base

A4 | KRALYN | Material: 6061 AL

For any Problems or errors,
please email

1.5;1 | 5/1/2022 | 2
+-0.25mm | Danning Liang

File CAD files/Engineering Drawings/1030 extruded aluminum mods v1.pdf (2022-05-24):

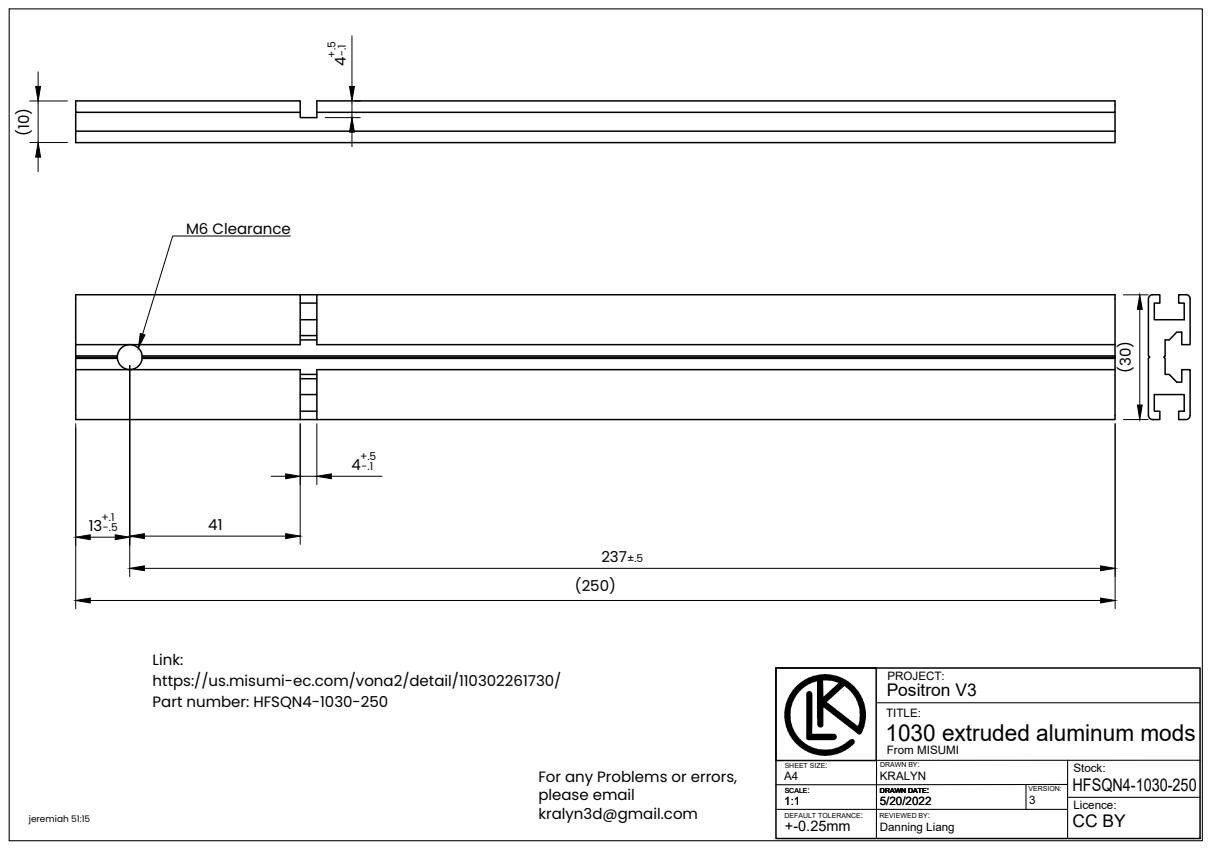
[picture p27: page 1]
DRAWN BY: SCALE:; DRAWN DATE:; VERSION: REVIEWED BY:; From MISUMI; Danning Liang (10); M6 Clearance; Part number: HFSQN4-1030-250; jeremiah 51:15

PROJECT:
Positron V3
1030 extruded aluminum mods

TITLE: SHEET SIZE: SCALE: DEFAULT TOLERANCE:

For any Problems or errors,
please email
kralyn3d@gmail.com

A4 | KRALYN | Stock: HFSQN4-1030-250

1:1 | 5/20/2022 | 3
+-0.25mm

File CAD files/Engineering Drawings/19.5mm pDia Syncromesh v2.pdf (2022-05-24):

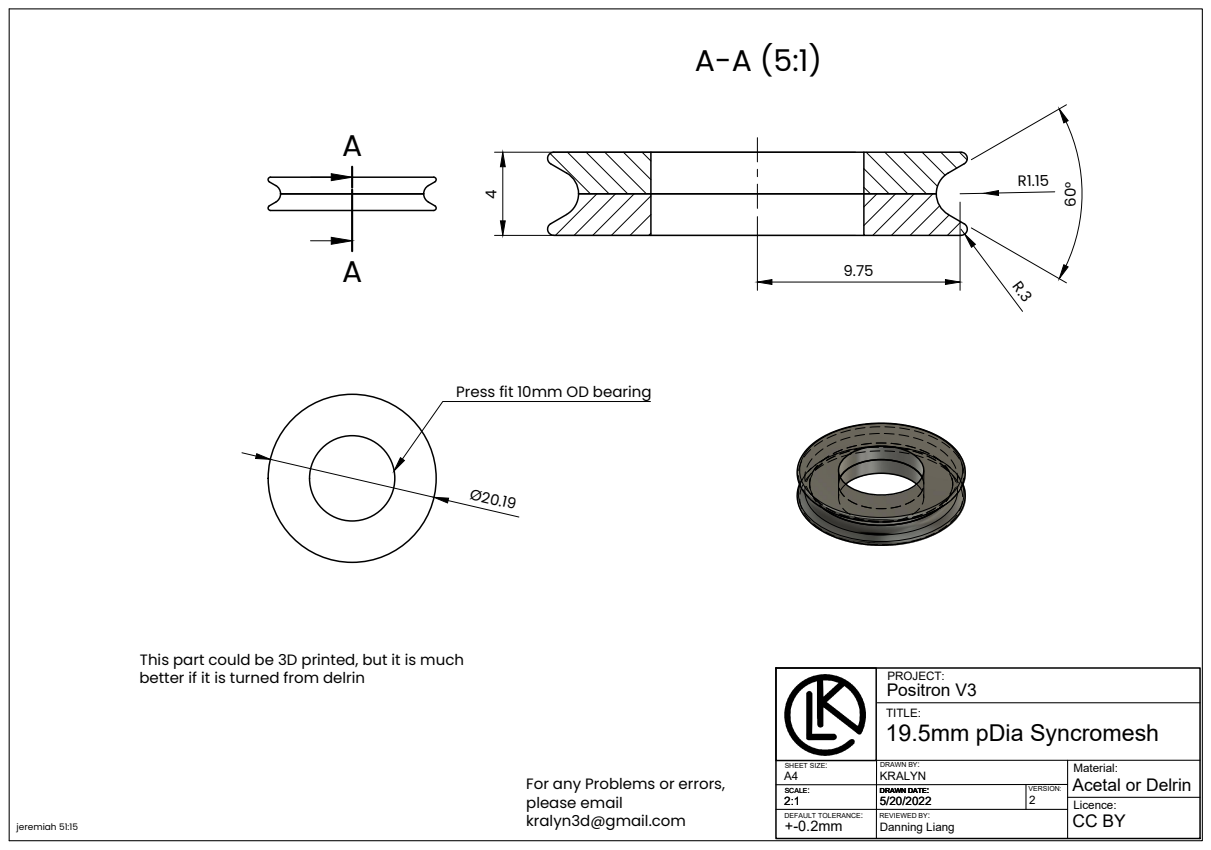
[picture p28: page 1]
DRAWN BY: SCALE:; DRAWN DATE:; VERSION: REVIEWED BY:; Positron V3; 19.5mm pDia Syncromesh; jeremiah 51:15

Press fit 10mm OD bearing

This part could be 3D printed, but it is much
better if it is turned from delrin

TITLE: SHEET SIZE: SCALE: DEFAULT TOLERANCE:

A4 | KRALYN | Material: Acetal or Delrin

For any Problems or errors,
please email
kralyn3d@gmail.com

2:1 | 5/20/2022 | 2
+-0.2mm | Danning Liang

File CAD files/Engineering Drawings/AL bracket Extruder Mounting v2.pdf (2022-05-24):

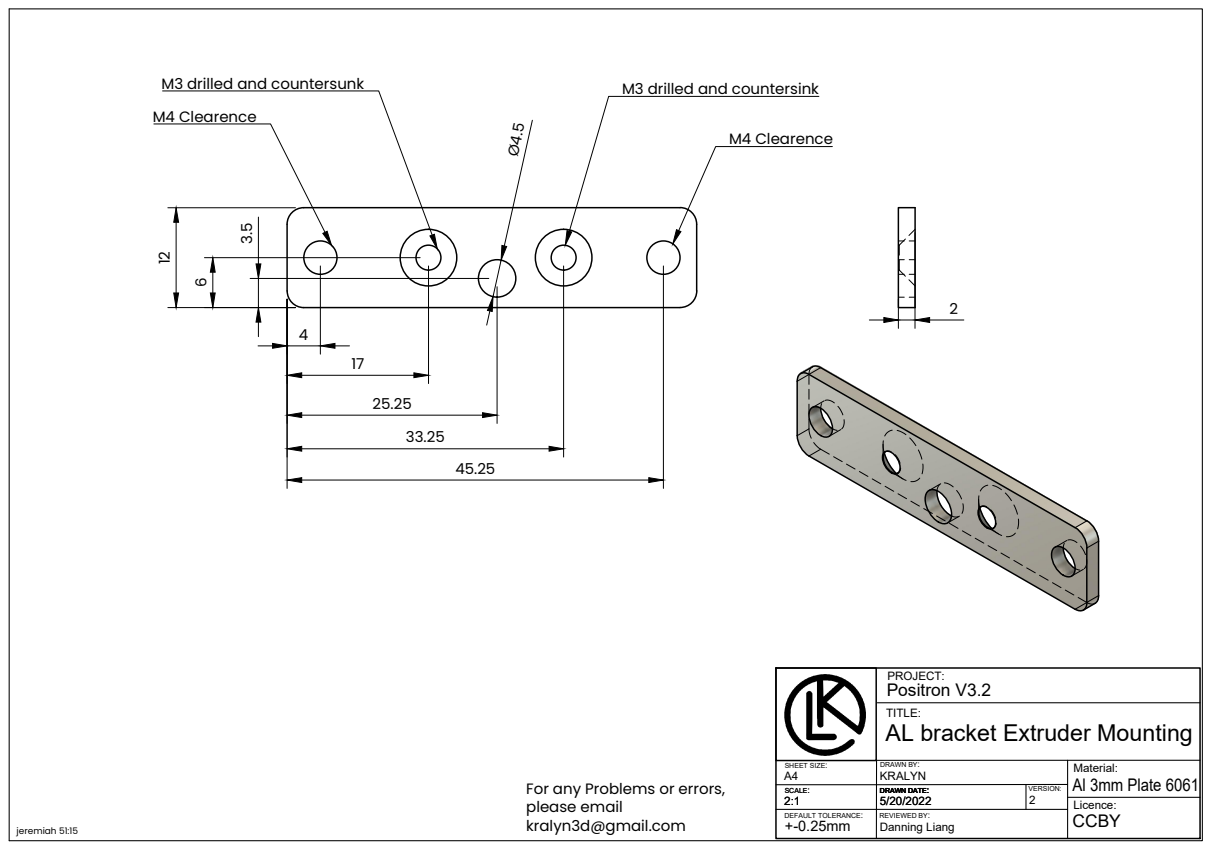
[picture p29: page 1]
DRAWN BY: SCALE:; DRAWN DATE:; VERSION: REVIEWED BY:; Danning Liang 12; M4 Clearence; M3 drilled and countersunk; M3 drilled and countersink; jeremiah 51:15; kralyn3d@gmail.com

PROJECT:
Positron V3.2
AL bracket Extruder Mounting

TITLE: SHEET SIZE: SCALE: DEFAULT TOLERANCE:

A4 | KRALYN | Material: Al 3mm Plate 6061

For any Problems or errors,
please email

2:1 | 5/20/2022 | 2
+-0.25mm

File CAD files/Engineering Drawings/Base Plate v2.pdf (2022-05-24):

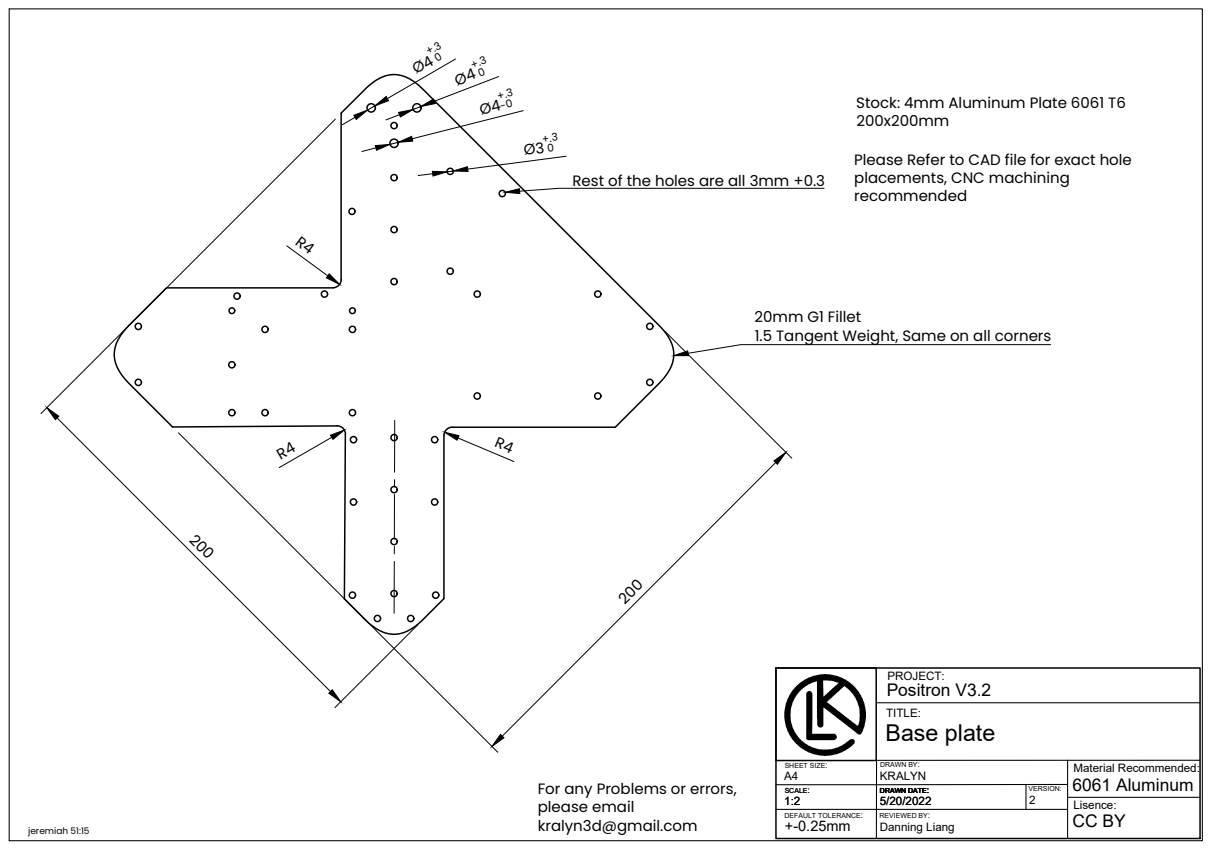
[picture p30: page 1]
DRAWN BY: SCALE:; DRAWN DATE:; VERSION: REVIEWED BY:; Positron V3.2; Base plate; jeremiah 51:15; kralyn3d@gmail.com

Stock: 4mm Aluminum Plate 6061 T6
Please Refer to CAD file for exact hole
placements, CNC machining
recommended

Rest of the holes are all 3mm +0.3

20mm G1 Fillet
1.5 Tangent Weight, Same on all corners

TITLE: SHEET SIZE: SCALE: DEFAULT TOLERANCE:

A4 | KRALYN | Material Recommended: 6061 Aluminum

For any Problems or errors,
please email

1:2 | 5/20/2022 | 2
+-0.25mm | Danning Liang

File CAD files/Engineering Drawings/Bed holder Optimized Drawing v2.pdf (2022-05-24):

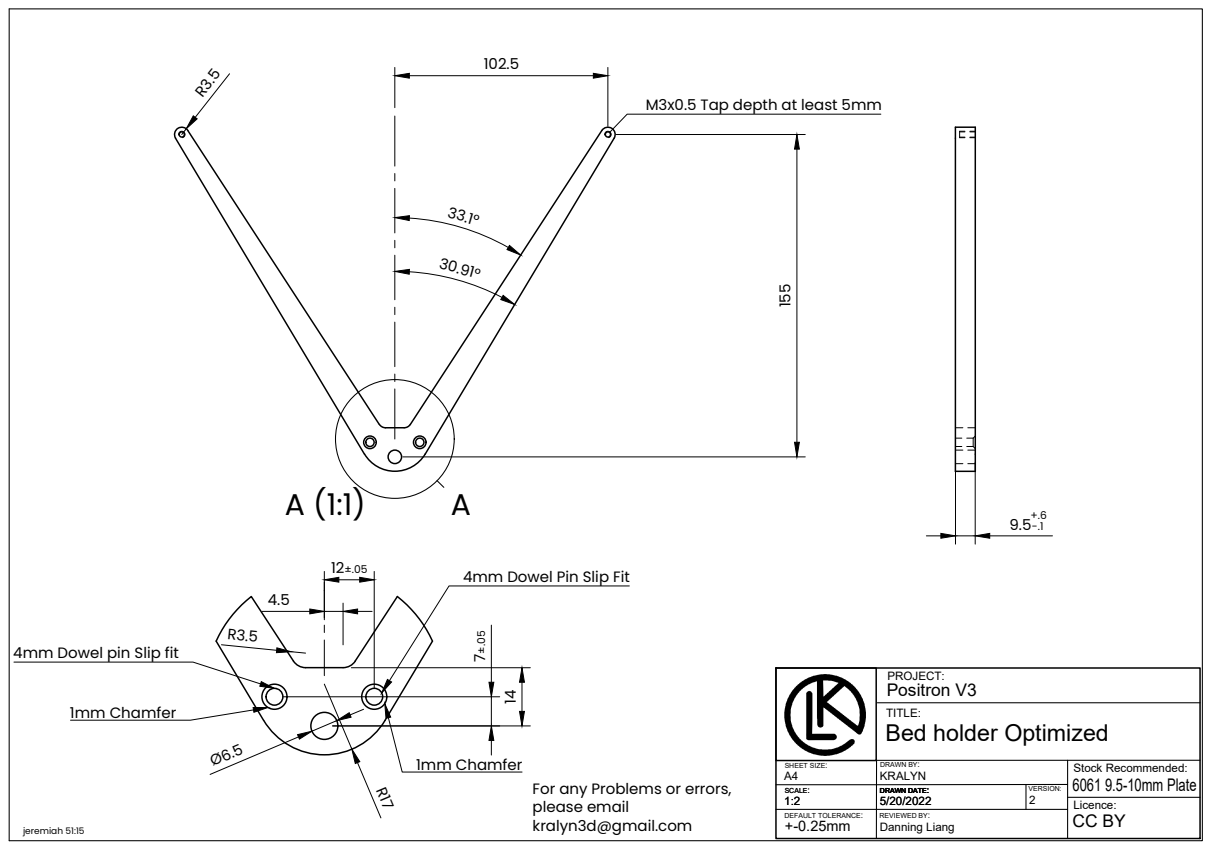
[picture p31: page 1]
DRAWN BY: SCALE:; DRAWN DATE:; VERSION: REVIEWED BY:; jeremiah 51:15; kralyn3d@gmail.com; 1mm Chamfer

M3x0.5 Tap depth at least 5mm 14

4mm Dowel Pin Slip Fit

4mm Dowel pin Slip fit

PROJECT:
Positron V3
Bed holder Optimized

TITLE: SHEET SIZE: SCALE: DEFAULT TOLERANCE:

A4 | KRALYN | Stock Recommended: 6061 9.5-10mm Plate

For any Problems or errors,
please email

1:2 | 5/20/2022 | 2
+-0.25mm | Danning Liang

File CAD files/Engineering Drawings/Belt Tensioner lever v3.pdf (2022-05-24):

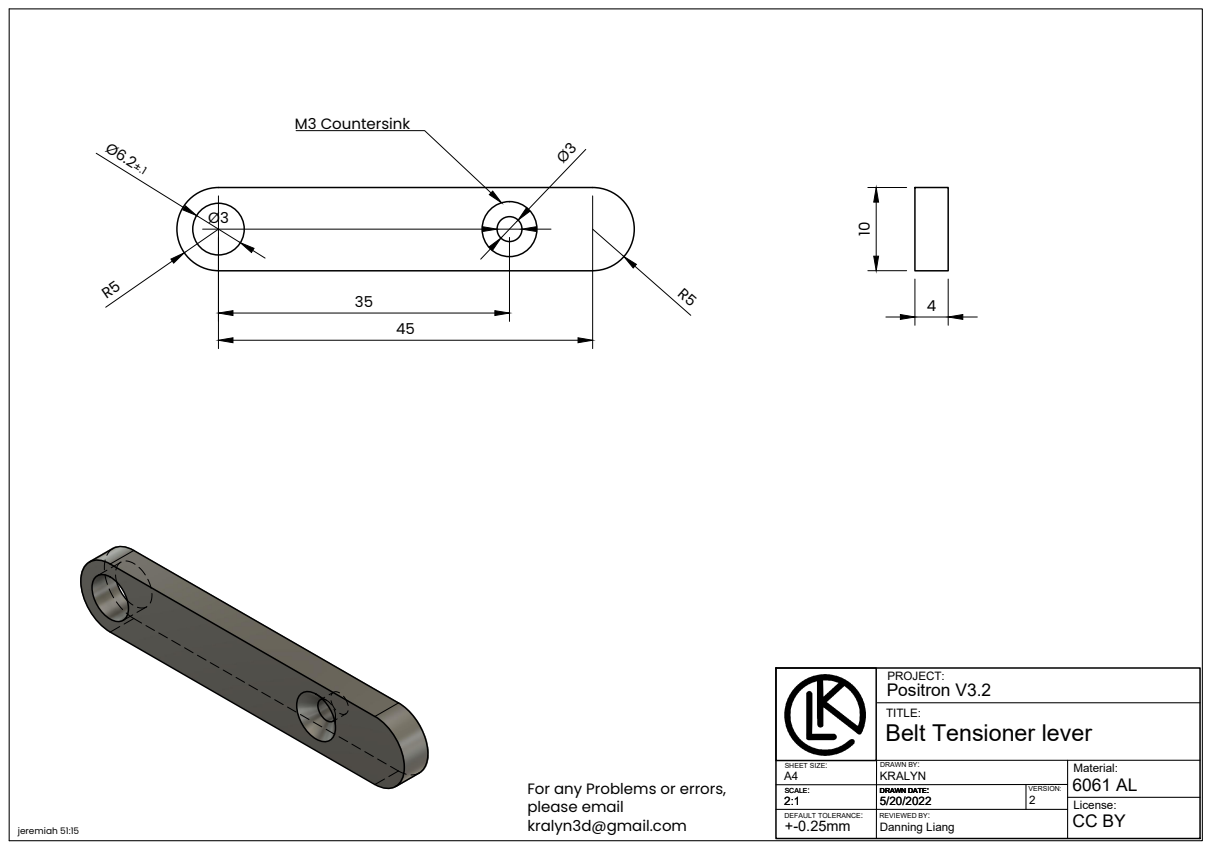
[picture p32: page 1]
DRAWN BY: SCALE:; DRAWN DATE:; VERSION: REVIEWED BY:; M3 Countersink; jeremiah 51:15; kralyn3d@gmail.com

PROJECT:
Positron V3.2
Belt Tensioner lever

TITLE: SHEET SIZE: SCALE: DEFAULT TOLERANCE:

A4 | KRALYN | Material: 6061 AL

For any Problems or errors,
please email

2:1 | 5/20/2022 | 2
+-0.25mm | Danning Liang

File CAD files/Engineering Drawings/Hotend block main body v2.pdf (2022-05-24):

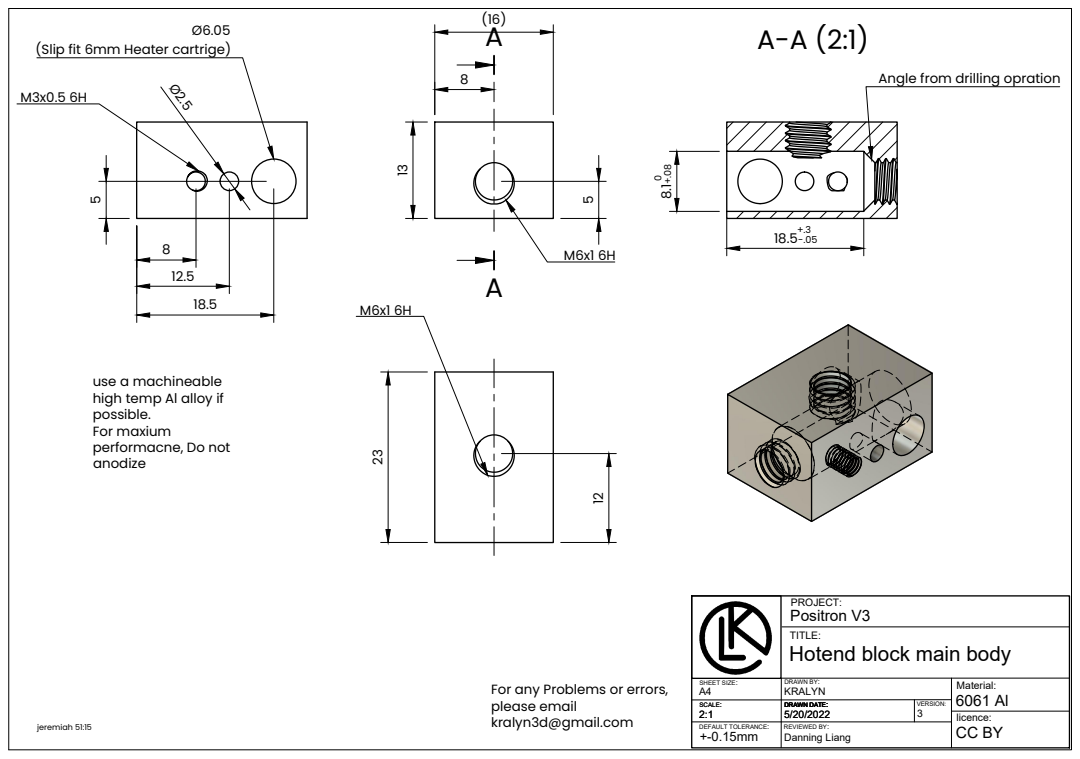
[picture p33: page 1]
DRAWN BY: SCALE:; DRAWN DATE:; VERSION: REVIEWED BY:; (Slip fit 6mm Heater cartrige); jeremiah 51:15

Angle from drilling opration

use a machineable
high temp Al alloy if
possible.
For maxium
performacne, Do not
anodize

PROJECT:
Positron V3
Hotend block main body

TITLE: SHEET SIZE: SCALE: DEFAULT TOLERANCE:

For any Problems or errors,
please email
kralyn3d@gmail.com

A4 | KRALYN | Material: 6061 Al

2:1 | 5/20/2022 | 3
+-0.15mm | Danning Liang

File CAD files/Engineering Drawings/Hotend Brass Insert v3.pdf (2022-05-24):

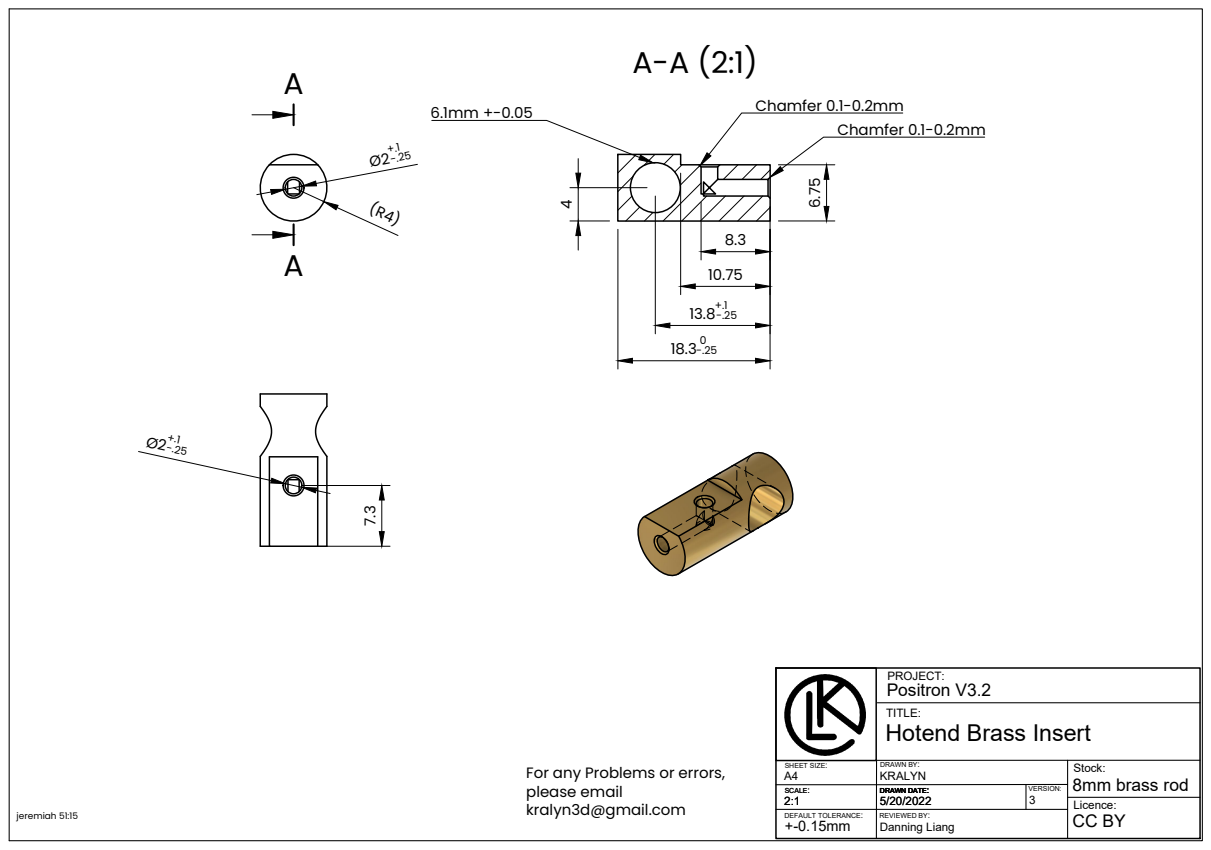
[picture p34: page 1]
DRAWN BY: SCALE:; DRAWN DATE:; VERSION: REVIEWED BY:; Chamfer 0.1-0.2mm; Chamfer 0.1-0.2mm 6.75; jeremiah 51:15; kralyn3d@gmail.com

PROJECT:
Positron V3.2
Hotend Brass Insert

TITLE: SHEET SIZE: SCALE: DEFAULT TOLERANCE:

For any Problems or errors,
please email

A4 | KRALYN | Stock: 8mm brass rod

2:1 | 5/20/2022 | 3
+-0.15mm | Danning Liang

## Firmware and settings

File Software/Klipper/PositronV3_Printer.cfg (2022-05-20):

[printer]
kinematics: corexy
max_velocity: 350
max_accel: 8000
max_accel_to_decel: 7000
square_corner_velocity: 7
max_z_velocity: 50
max_z_accel: 150

[stepper_y]
step_pin: gpio11
dir_pin: !gpio10
enable_pin: !gpio12
microsteps: 16
rotation_distance: 57.1
#endstop_pin: ^gpio4
endstop_pin: tmc2209_stepper_y:virtual_endstop
homing_retract_dist: 0
position_endstop: 0
position_max: 176
homing_speed: 15

[tmc2209 stepper_y]
uart_pin: gpio9
tx_pin: gpio8
uart_address: 0
run_current: 0.7
stealthchop_threshold: 999999
diag_pin: ^gpio4
driver_SGTHRS: 17

[stepper_x]
step_pin: gpio6
dir_pin: !gpio5
enable_pin: !gpio7
microsteps: 16
rotation_distance: 57.1
#endstop_pin: ^gpio3
endstop_pin: tmc2209_stepper_x:virtual_endstop
homing_retract_dist: 0
position_endstop: 0
position_max: 185
homing_speed: 15

[tmc2209 stepper_x]
uart_pin: gpio9
tx_pin: gpio8
uart_address: 2
run_current: 0.7
stealthchop_threshold: 999999
diag_pin: ^gpio3
driver_SGTHRS: 20

[stepper_z]
step_pin: gpio19
dir_pin: gpio28
enable_pin: !gpio2
microsteps: 16
rotation_distance: 6.6667
endstop_pin: probe:z_virtual_endstop
position_min: -2.0
position_max: 181
homing_speed: 12

[tmc2209 stepper_z]
uart_pin: gpio9
tx_pin: gpio8
uart_address: 1
run_current: 0.22
stealthchop_threshold: 999999

[extruder]
step_pin: gpio14
dir_pin: gpio13
enable_pin: !gpio15
microsteps: 16
rotation_distance: 4.92
nozzle_diameter: 0.4
filament_diameter: 1.75
heater_pin: gpio21
sensor_type: Generic 3950
sensor_pin: gpio27
control: pid
pid_Kp: 25.12
pid_Ki: 1.073
pid_Kd: 147
min_temp: -100
max_temp: 255
max_extrude_cross_section:2
pressure_advance: 0.18 #0.18
min_extrude_temp: 170
max_extrude_only_distance: 400

[tmc2209 extruder]
uart_pin: gpio9
tx_pin: gpio8
uart_address: 3
run_current: 0.69
hold_current: 0.4
stealthchop_threshold: 999999

[heater_bed]
heater_pin: gpio23
sensor_type: Generic 3950
sensor_pin: gpio26
pwm_cycle_time: 0.015
max_power: 0.8
control: pid
pid_Kp: 56.852
pid_Ki: 2.1
pid_Kd: 383.75
min_temp: -100
max_temp: 85

[controller_fan mcu_fan]
pin: gpio17
max_power: 0.8
shutdown_speed: 0
#cycle_time: 0.01
kick_start_time: 1
fan_speed: 0.8
idle_timeout: 5
stepper: stepper_x, stepper_y, stepper_z


[heater_fan nozzle_cooling_fan]
pin: gpio20
kick_start_time: 1

[fan]
pin: gpio18
kick_start_time: 1


[mcu]
serial: /dev/ttyAMA0
baud: 250000
restart_method: command

[force_move]
enable_force_move = true

[gcode_macro FORCE_Z_UP]
gcode: FORCE_MOVE STEPPER=stepper_z DISTANCE=30 VELOCITY=40

[virtual_sdcard]
path: ~/gcode_files

[safe_z_home]
home_xy_position: 90,90 # Change coordinates to the center of your print bed
speed: 100
z_hop: 3                # Move up 5mm
z_hop_speed: 5

[probe]
pin: ^gpio25
x_offset:-46
y_offset: -37
z_offset: 0.8
speed: 3
samples: 3
sample_retract_dist: 0.7

[bed_tilt]
points: 
  55,31
  175,31
  175,175
  55,175
speed: 150
horizontal_move_z: 4

[gcode_macro UNLOAD_FILAMENT]
gcode = 
  M83 
  G1 E-30 F1800
  G1 E-100 F1200
  G1 E-100 F1200
  G1 E-100 F1200
  G1 E-100 F1200
  G92 E0
  G90

[gcode_macro LOAD_FILAMENT]
gcode = 
  M83 
  G1 E100 F1200
  G1 E100 F1200
  G1 E100 F1200
  G1 E100 F1200
  G1 E20 F600
  G92 E0
  G90
  



[gcode_macro G29]
gcode = 
  G28
  G1 Z5 F800
	BED_TILT_CALIBRATE

[delayed_gcode my_delayed_gcode]
gcode:
    SET_LED LED=WS2812 RED=0 GREEN=0.05 BLUE=0.01 INDEX=3
    SET_LED LED=WS2812 RED=0.1 GREEN=0.1 BLUE=0.05 INDEX=2
    SET_LED LED=WS2812 RED=0.1 GREEN=0.1 BLUE=0.05 INDEX=1
    G4 P100
    SET_LED LED=WS2812 RED=0 GREEN=0.1 BLUE=0.02 INDEX=3
    SET_LED LED=WS2812 RED=0.2 GREEN=0.2 BLUE=0.1 INDEX=2
    SET_LED LED=WS2812 RED=0.2 GREEN=0.2 BLUE=0.1 INDEX=1
    G4 P100
    SET_LED LED=WS2812 RED=0 GREEN=0.15 BLUE=0.04 INDEX=3
    SET_LED LED=WS2812 RED=0.3 GREEN=0.3 BLUE=0.15 INDEX=2
    SET_LED LED=WS2812 RED=0.3 GREEN=0.3 BLUE=0.15 INDEX=1
    G4 P100
    SET_LED LED=WS2812 RED=0 GREEN=0.2 BLUE=0.05 INDEX=3
    SET_LED LED=WS2812 RED=0.4 GREEN=0.4 BLUE=0.2 INDEX=2
    SET_LED LED=WS2812 RED=0.4 GREEN=0.4 BLUE=0.2 INDEX=1
    G4 P100
    SET_LED LED=WS2812 RED=0 GREEN=0.3 BLUE=0.1 INDEX=3
    SET_LED LED=WS2812 RED=0.5 GREEN=0.5 BLUE=0.25 INDEX=2
    SET_LED LED=WS2812 RED=0.5 GREEN=0.5 BLUE=0.25 INDEX=1
    G4 P100
    SET_LED LED=WS2812 RED=0.6 GREEN=0.6 BLUE=0.3 INDEX=2
    SET_LED LED=WS2812 RED=0.6 GREEN=0.6 BLUE=0.3 INDEX=1
    G4 P100
    SET_LED LED=WS2812 RED=0.7 GREEN=0.7 BLUE=0.35 INDEX=2
    SET_LED LED=WS2812 RED=0.7 GREEN=0.7 BLUE=0.35 INDEX=1
    G4 P100
    SET_LED LED=WS2812 RED=0.9 GREEN=0.9 BLUE=0.45 INDEX=2
    SET_LED LED=WS2812 RED=0.9 GREEN=0.9 BLUE=0.45 INDEX=1
initial_duration: 0.1

[pause_resume]

[gcode_macro CANCEL_PRINT]
rename_existing: BASE_CANCEL_PRINT
gcode:
  TURN_OFF_HEATERS
  CLEAR_PAUSE
  SDCARD_RESET_FILE
  G91 E0
  G1 E-1.0 F240
  G92 E0
  G1 X5 Y5 F3000
  G91
  G1 Z25 F800
  G1 Z25 F800
  G1 Z25 F800
  G90

  BASE_CANCEL_PRINT

[gcode_macro RESUME]
rename_existing: BASE_RESUME
gcode:
  ##### read E from pause macro #####
  {% set E = printer["gcode_macro PAUSE"].extrude|float %}
  ##### end of definitions #####
  G91
  G1 E{E} F240
  RESTORE_GCODE_STATE NAME=PAUSE_state
  BASE_RESUME

[gcode_macro PAUSE]
rename_existing: BASE_PAUSE
# change this if you need more or less extrusion
variable_extrude: 1.0
gcode:
  ##### read E from pause macro #####
  {% set E = printer["gcode_macro PAUSE"].extrude|float %}
  ##### set park positon for x and y #####
  # default is your max posion from your printer.cfg
  {% set x_park = printer.toolhead.axis_maximum.x|float - 10.0 %}
  {% set y_park = printer.toolhead.axis_maximum.y|float - 10.0 %}
  ##### calculate save lift position #####
  {% set max_z = printer.toolhead.axis_maximum.z|float %}
  {% set act_z = printer.toolhead.position.z|float %}
  {% if act_z < (max_z - 2.0) %}
      {% set z_safe = 2.0 %}
  {% else %}
      {% set z_safe = max_z - act_z %}
  {% endif %}
  ##### end of definitions #####
  SAVE_GCODE_STATE NAME=PAUSE_state
  BASE_PAUSE
  G91
  G1 E-{E} F240
  G1 Z{z_safe} F900
  G90
  G1 X{x_park} Y{y_park} F5000

[neopixel WS2812]
pin: gpio24
chain_count: 5
color_order: GRB
initial_RED: 0.0
initial_GREEN: 0.0
initial_BLUE: 0.0

[display_status] 

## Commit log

2022-05-20 Change License to CC BY
    Change License to CC BY
    [1030 extruded aluminum.step, 15mm pDia Synchromesh.stl, 19.5mm pDia Synchromesh.stl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]
2022-05-20 Updating files and rename erroneous files
    Updating files and rename erroneous files
    [15mm pDia Synchromesh.stl, BOM_PCB_Positron V3 PCB_2022-05-20.csv, Hotend block main body.step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]
2022-05-21 Updating errors in BOM
    Updating errors in BOM
    [PositronV3.2 BOM V2.xlsx, PositronV3.2 BOM.xlsx]
2022-05-21 updated ReadME.md and removed tracking metadata from BOM links.
    [PositronV3.2 BOM V2 - old.xlsx, Positron_V3.2_BOM.csv, Positron_V3.2_BOM.xlsx]
2022-05-21 Fixed BOM errors
    Fixed description for magsafe connector
    Added HNTT5 T nut which was missing.
    [PositronV3.2 BOM V3.xlsx, Positron_V3.2_BOM.csv, Positron_V3.2_BOM.xlsx]
2022-05-21 Update BOM, logo
    Added missing brass insert in BOM as well as T nuts. Updated Positron Logo to the current one
    [Positron V3 Logo v2.dxf, PositronV3.2 BOM V4.xlsx, Positron_V3.2_BOM.xlsx]
2022-05-21 Fix some typos, multiply BOM price by quantity, formatting
    [PositronV3.2 BOM V4.xlsx]
2022-05-22 Revert "Fix some typos, multiply BOM price by quantity, formatting"
    [PositronV3.2 BOM V4.xlsx]
2022-05-24 Changing file structure, updating various files
    Positron V3.2 Design Files change Log 2020/5/24
    Added KRALYN Design and Positron Logo to CAD design
    Added Drawing for Synchrmehs cable instructions
    Changed Z axis Holder Block from 30mm width to 29.5mm for extra clearance.
    Changed the Film heater version of the bed to the correct orientation.
    Renamed M4 spacer 4.1mmx6 into Z axis belt tensioner arm hinge spacer.
    Minor logo updates
    Changed BOM Location to Google Sheets
    Added several other links to productions etc.
    Split Pulley Holder Bottom STL
    Reduced height of SpoolHolders by 1mm
    Added SpoolHolders to 3D printed model Stls
    Added Thumbscrew M6 Z axis custom drawing
    Added Thumbscrew M6 Z axis cu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
    [1030 extruded aluminum.step, 90 degree Bed Holder.step, 90 degree angled aluminum.step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]
2022-05-24 Create Z axis Holder Block v2.pdf
2022-06-21 updated 90 degree bed holder
    Changed Logo and updated 90 degree bed holder drawings
    [KL Logo KRALYN Design CAD v1.step, KL Logo KRALYN Design v1.dxf, Side Panel Right XT 60.stl]
2022-07-17 After Testing of the tnesioning end holder block mod by MelonColley, some updates were done. 1st, it allows the use of either a m3 insert, or a m3 nut. And 2nd, 2 versions have been created. One is a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
    This is not mature and ready for a PR to the main postron repo.
    (cherry picked from commit f7362c53b1878ef255b17b17fd888f8a5c18f75c)
    [End Holder Block - Tensioning Mod, 1 part, moving ledges.stp, End Holder Block - Tensioning Mod, Fixed Ledges.stp, Z axis Holder block.prt]
2022-07-17 Angled Extruder to pull filament from behind, no slot in z extrudion required
2022-07-22 updating pull requests,
    [End Holder Block - Tensioning Mod, 1 part, moving ledges.stp, End Holder Block - Tensioning Mod, Fixed Ledges.stp, Z axis Holder block.prt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]
2023-02-02 Improovment adn update to the angeld extruder mod
2024-05-01 Rename Positron V3.2 Rev B v56.f3z to Positron V3.2 (LEGACY) Rev B v56.f3z
    [Positron V3.2 (LEGACY) Rev B v56.f3z]
